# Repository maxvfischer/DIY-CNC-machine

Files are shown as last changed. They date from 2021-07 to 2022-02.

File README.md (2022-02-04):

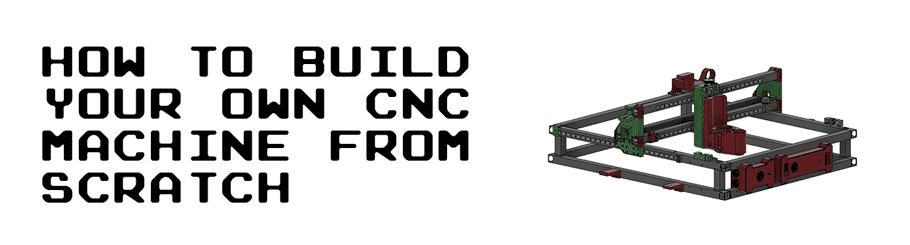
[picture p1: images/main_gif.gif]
main_gif


This guide goes through all the steps to build your own CNC machine from scratch. It includes a complete bill of materials (BOM), STL/OBJ-files for all the 3d-printed parts and detailed instructions of how everything is assembled. It also includes instructions of how all the necessary open-source softwares are installed.

The guide is based on Ivan Miranada's design and is a complement to Ivan's Youtube-videos:

1. Original video: [https://www.youtube.com/watch?v=_atw3e0nIrg](https://www.youtube.com/watch?v=_atw3e0nIrg)
2. Updates with geared stepper motors etc: [https://www.youtube.com/watch?v=qpjf5D3WngY](https://www.youtube.com/watch?v=qpjf5D3WngY)
3. Updating to metal parts: [https://www.youtube.com/watch?v=RDnGvhdGFEY](https://www.youtube.com/watch?v=RDnGvhdGFEY)

If you have any questions, feel free to contact me on LinkedIn: [https://www.linkedin.com/in/max-fischer-92997281/](https://www.linkedin.com/in/max-fischer-92997281/) 

or

contact

cnc_top_gif

---

**Featured on**

* Hackernews (#2): [https://news.ycombinator.com/item?id=29096954](https://news.ycombinator.com/item?id=29096954)
* Console open-source newsletter: [https://console.substack.com/p/console-83](https://console.substack.com/p/console-83)
* Hackaday's blog: [https://hackaday.com/2021/11/05/diy-cnc-uses-lots-of-3d-printed-parts/](https://hackaday.com/2021/11/05/diy-cnc-uses-lots-of-3d-printed-parts/)
* Hackaday's podcast (~25:30): [https://open.spotify.com/episode/2YuxrVAgbQvVTjcUljJ3rj?si=lkp1L061R7ix6WkA7s1ieA](https://open.spotify.com/episode/2YuxrVAgbQvVTjcUljJ3rj?si=lkp1L061R7ix6WkA7s1ieA)
* Arduino's official blog: [https://blog.arduino.cc/2021/11/03/learn-how-to-build-your-own-massive-3d-printed-cnc-router/](https://blog.arduino.cc/2021/11/03/learn-how-to-build-your-own-massive-3d-printed-cnc-router/)
* Weekly robotics newsletter: [https://weeklyrobotics.com/weekly-robotics-168](https://weeklyrobotics.com/weekly-robotics-168)

---

# Table of content
1. [License](#license)
2. [Parts (bill of materials)](#parts-bill-of-materials)
3. [Build the CNC machine](#build-the-CNC-machine)
	1. [Main frame](#main-frame)
		1. [Drill holes in 900 mm profiles](#drill-holes-in-900-mm-profiles)
		2. [Rails to 900 mm profiles](#rails-to-900-mm-profiles)
		3. [Assemble upper and lower frames](#assemble-upper-and-lower-frames)
		4. [Interlock upper and lower frames](#interlock-upper-and-lower-frames)
	2. [Y-axis](#y-axis)
		1. [Side plates to upper frame](#side-plates-to-upper-frame)
		2. [Y-axis motors, idlers and pulleys to side plates](#y-axis-motors-idlers-and-pulleys-to-side-plates)
		3. [Y-axis belt tensioners and end-stop mounts](#y-axis-belt-tensioners-and-end-stop-mounts)
		4. [Y-axis HTD5M belts](#y-axis-htd5m-belts)
	3. [X-axis and Z-axis](#x-axis-and-z-axis)
		1. [Rails to bridge beams](#rails-to-bridge-beams)
		2. [X-axis tensioner and end-stop mount to lower bridge beam](#x-axis-tensioner-and-end-stop-mount-to-lower-bridge-beam)
		3. [Bridge beams to side plates](#bridge-beams-to-side-plates)
		4. [Rod bearings to carriage](#rod-bearings-to-carriage)
		5. [Carriage to bridge beams](#carriage-to-bridge-beams)
		6. [X-axis motor, idlers and pulley to carriage](#x-axis-motor-idlers-and-pulley-to-carriage)
		7. [X-axis HTD5M belt](#x-axis-htd5m-belt)
		8. [Acme nut and rails to carriage slider](#acme-nut-and-rails-to-carriage-slider)
		9. [Acme rod and vertical slider to carriage](#acme-rod-and-vertical-slider-to-carriage)
		10. [Z motor mount and X-axis cable chain](#z-motor-mount-and-X-axis-cable-chain)
		11. [Y-axis cable chain](#y-axis-cable-chain)
		12. [Z stepper motor, pulleys and belt](#z-stepper-motor-pulleys-and-belt)
	4. [Stepper motors and end-stops](#stepper-motors-and-end-stops)
		1. [Extend stepper motor wires](#extend-stepper-motor-wires)
			1. [Y-axis 1](#y-axis-1)
			2. [Y-axis 2](#y-axis-2)
			3. [X-axis](#x-axis)
			4. [Z-axis](#z-axis)
		2. [End-stops and end-stop wires](#end-stops-and-end-stop-wires)
			1. [X-axis (max)](#x-axis-max)
			2. [X-axis (min)](#x-axis-min)
			3. [Y-axis (max)](#y-axis-max)
			4. [Y-axis (min)](#y-axis-min)
			5. [Z-axis (max)](#z-axis-max)
		3. [Stepper motor and end-stop cable management](#stepper-motor-and-end-stop-cable-management)
			1. [Y-axis steppers and X-axis end-stops](#y-axis-steppers-and-x-axis-end-stops)
			2. [X-axis stepper, Z-axis stepper and Z-axis end-stop](#x-axis-stepper-Z-axis-stepper-and-z-axis-end-stop)
	5. [Router](#router)
		1. [Attach router to carriage](#attach-router-to-carriage)
		2. [Router cable management](#router-cable-management)
	6. [Electronic boxes](#electronic-boxes)
		1. [Small electronic box](#small-electronic-box)
		2. [Large electronic box](#large-electronic-box)
	7. [Electrical wiring and connect components](#electrical-wiring-and-connect-components)
		1. [Main power supply](#main-power-supply)
		2. [Prepare power to steppers and connect fans and LED](#prepare-power-to-steppers-and-connect-fans-and-LED)
		3. [Assemble stepper motor drivers and tune VRef](#assemble-stepper-motor-drivers-and-tune-vref)
		4. [Attach Arduino and solder USB cable](#attach-arduino-and-solder-usb-cable)
		5. [Stepper and end-stop cable management to small electronic box](#stepper-and-end-stop-cable-management-to-small-electronic-box)
		6. [Connect steppers to CNC shield](#connect-steppers-to-cnc-shield)
		7. [Connect end-stops to CNC shield](#connect-end-stops-to-cnc-shield)
		8. [Set microstepping](#set-microstepping)
		9. [Router cable management and connect to main power supply](#router-cable-management-and-connect-to-main-power-supply)
		10. [Final test of electrical wiring](#final-test-of-electrical-wiring)
	8. [Wasteboard](#wasteboard)
		1. [Cut out wasteboard](#cut-out-wasteboard)
		2. [Attach wasteboard to CNC](#attach-wasteboard-to-cnc)
	9. [Dust shoe (updated Feb 4, 2022)](#dust-shoe-updated-feb-4-2022)
4. [Software](#software)
	1. [Install CNC software (grbl) on Arduino Uno](#install-cnc-software-grbl-on-arduino-uno)
		1. [Install Arduino Software (IDE)](#install-arduino-software-ide)
		2. [Install GRBL](#install-grbl)
	2. [G-Code sender](#g-code-sender)
		1. [Install G-Code sender](#install-g-code-sender)
		2. [Connect G-Code sender to GRBL](#connect-g-code-sender-to-grbl)
		3. [Adjust GRBL configuration](#adjust-grbl-configuration)
			1. [Enable end-stops/hard limits](#enable-end-stopshard-limits)
			2. [Calculate and set travel resolutions](#calculate-and-set-travel-resolutions)
			3. [Other configurations](#other-configurations)
5. [Final notes](#final-notes)

# License
The following license is included when buying Ivan Miranda's blueprints of the CNC machine:

```
Everything that is in these files that I produced myself, apart from reselling the files, is allowed.
You can print and sell parts, sell machines, sell courses to build the machine. Modify the parts and post 
them for free, as long as you don’t sell the files and keep this license on everything you make with the 
files and credit me, we’re good. No DRM or anything, you are even allowed to repost the files as long as 
they’re kept free. Why buy this then? To support me and keep me encouraged to do more projects like this. 
```

Ivan does an amazing job putting these DIY builds together. I've posted his STL-files in this repository to simplify the build, but PLEASE buy his blueprints here: [https://ivanmiranda.com/products/3d-printed-cnc](https://ivanmiranda.com/products/3d-printed-cnc). It's only \$25 and helps him to continue build and share his awesome projects. Also, you will get access to a Discord channel that is really useful, where you can ask questions to a lot of people who have already built the machine.

Also, the Z-axis end-stop trigger, the ordinary end-stops and the rail supports all come from cello4's GitHub: [https://github.com/4cello/mirandacnc-community](https://github.com/4cello/mirandacnc-community).

# Parts (bill of materials)

**CLICK HERE TO OPEN THE BILL OF MATERIALS (BOM) MARKDOWN: [Bill of materials](./BILLOFMATERIAL.md)**

To simplify the build, I've created a separate markdown page with tables covering all parts needed to build the CNC-machine. The tables include a unique `Item No.` to easier refer to the parts in the guide. The tables also include images of all parts and .STL/.OBJ files of the parts that needs to be 3d-printed.

To get an even better understanding of how all the parts are used, I've created a detailed spreadsheet with comments:

* [On Google drive](https://docs.google.com/spreadsheets/d/1VdnPilA22OfAh9a1y4Ft6c2xkio206Dzv85h7AX7CmQ/edit?usp=sharing)
* [Bill\_of\_material.xlsx](./Bill_of_material.xlsx)

**To be able to continue with the build, you need to buy and 3d-print all needed parts found in the [bill of materials](./BILLOFMATERIAL.md).**

# Build the CNC machine
This section covers how all the parts is put together to build the CNC machine. 

All the measurements, distances and a complete overview of how everything comes together can be found in the main Fusion 360 CAD design. It can be downloaded here:

* [fusion\_360\_cad\_files.f3z](./fusion_360_cad_files.f3z)

Please note that the main Fusion 360 design is quite messy, which is one of the reasons why I've extracted the needed parts in a separate bill of materials.

Fusion 360 is a CAD program developed by Autodesk. It's free for personal use and can be downloaded here: [https://www.autodesk.com/products/fusion-360/personal](https://www.autodesk.com/products/fusion-360/personal). After you've downloaded Fusion 360, import `fusion_360_cad_files.f3z` to load the main CAD design. This can also come in handy if you need to adjust some of the 3d-printed parts.

## Main frame

### Drill holes in 900 mm profiles
The main frame consists of two separate frames, the lower and the upper frame. The two frames are kept together using threaded rods, washers and nuts. To enable the threaded rods to slide through the aluminium profiles, holes needed to be drilled.

First, a sharpie was used to indicate where all the holes were going in the 900mm profiles (**O07**). This was done by using a set square and a penn. A bradawl and a hammer were then used to make indentations at the center of the holes.

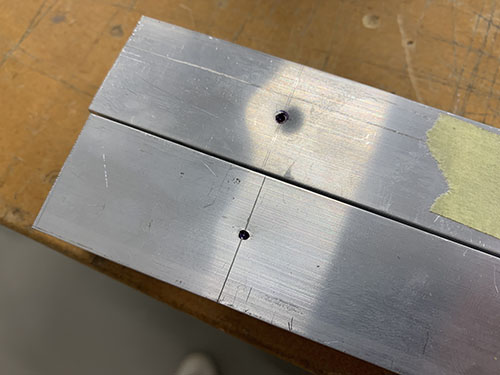
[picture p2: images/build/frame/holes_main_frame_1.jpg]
holes_main_frame_1


A 9 mm drill-bit and a bench drill was used to drill the holes straight through the profiles.

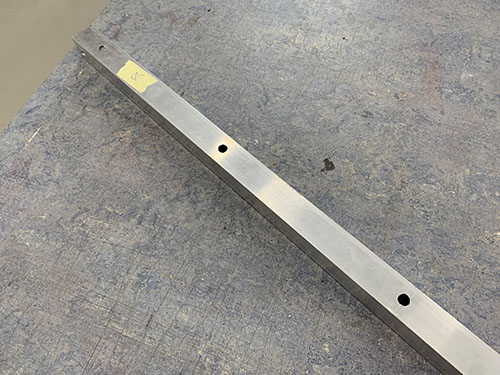
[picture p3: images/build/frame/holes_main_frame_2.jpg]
holes_main_frame_1


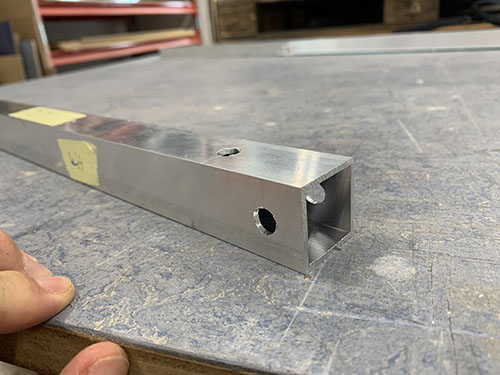
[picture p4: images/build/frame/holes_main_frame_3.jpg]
holes_main_frame_1


To be able to access the nuts and tight them with a socket wrench, some holes (facing outwards, see Fusion360 CAD file) needed to be enlarged. A sharpie was used to mark all the holes that needed to be enlarged.

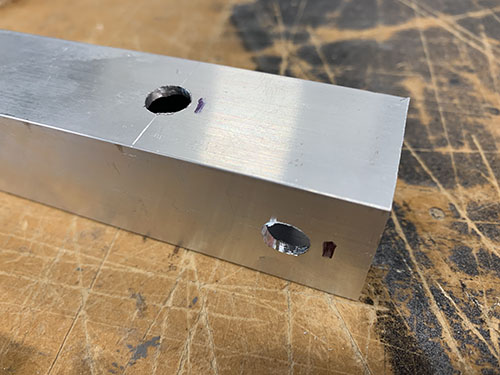
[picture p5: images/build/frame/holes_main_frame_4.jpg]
holes_main_frame_1


A step drill was then used to enlarge the holes holes to 20 mm. A tip is to measure the size of your socket wrench and keep the holes as small as possible, while you're still able to tighten the nuts. To be able to see which step you're aiming for on the step drill, attach a small piece of masking tape on the step above.

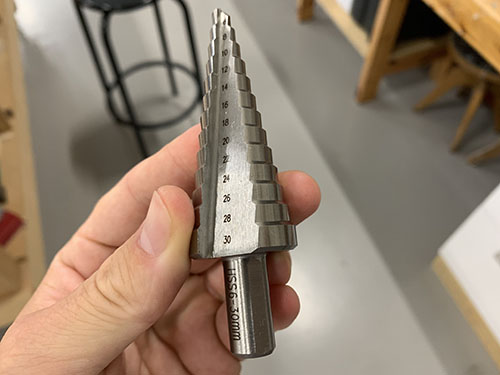
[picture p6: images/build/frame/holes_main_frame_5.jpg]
holes_main_frame_1


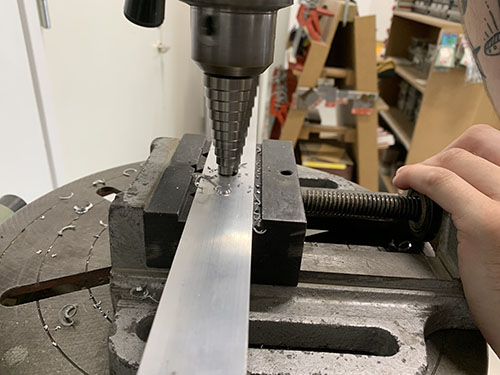
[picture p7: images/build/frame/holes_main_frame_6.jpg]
holes_main_frame_1


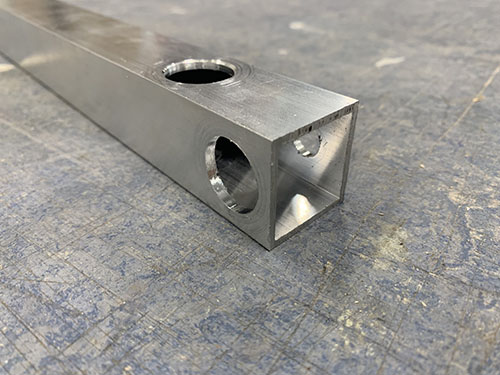
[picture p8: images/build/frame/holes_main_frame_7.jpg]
holes_main_frame_1


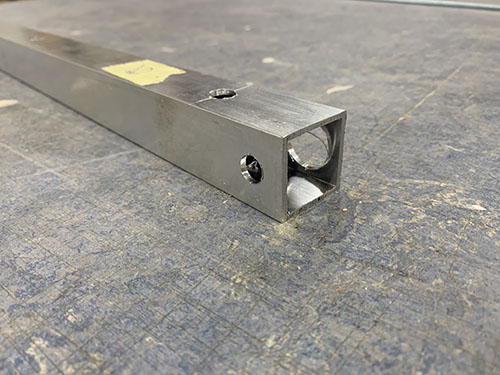
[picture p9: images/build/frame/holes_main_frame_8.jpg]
holes_main_frame_1


The edges were finally smoothed out using a round metal file.

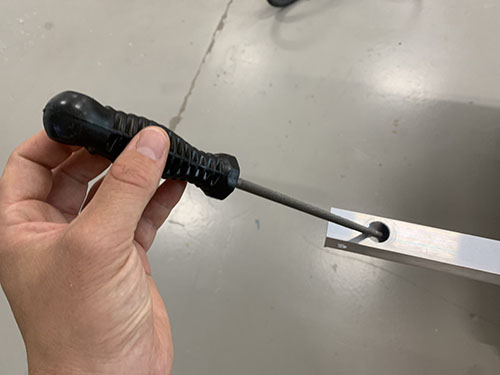
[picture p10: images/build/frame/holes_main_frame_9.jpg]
holes_main_frame_1


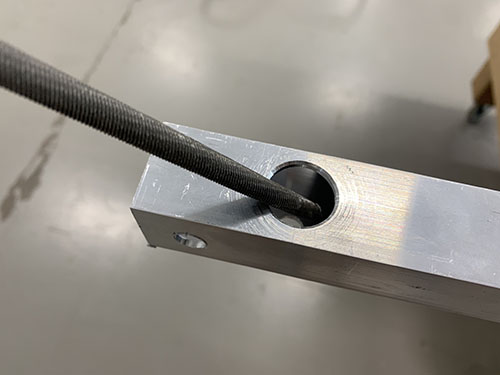
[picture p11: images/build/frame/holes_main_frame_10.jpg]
holes_main_frame_1


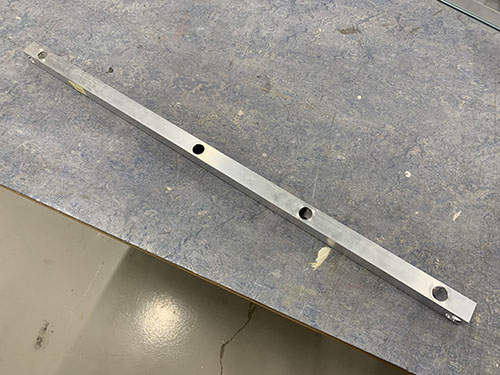
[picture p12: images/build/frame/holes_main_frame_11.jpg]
holes_main_frame_1


### Rails to 900 mm profiles

Before the upper and lower frames were assembled, two 600 mm MGN12H rails (**O21**) were attached to the 900 mm aluminium profiles (**O07**) of the **upper** frame. They were attached to the sides facing outwards and above the three 80 mm vertical beams (connecting the lower and upper frame). A tip is to place all the profiles as they should go to make sure that you're attaching the rails to the correct faces (see the red boxes on the image below). Also, be very careful when removing the MGN12H blocks (**O22**) from the rails.

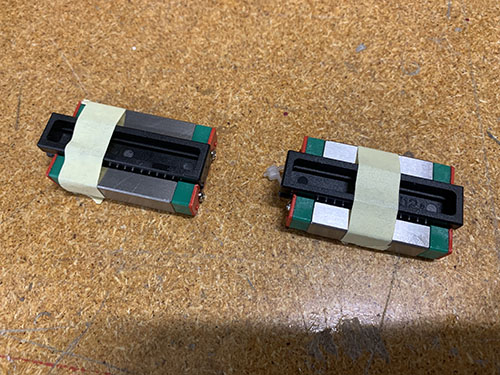
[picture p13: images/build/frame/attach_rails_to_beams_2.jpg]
attach_rails_to_beams_2


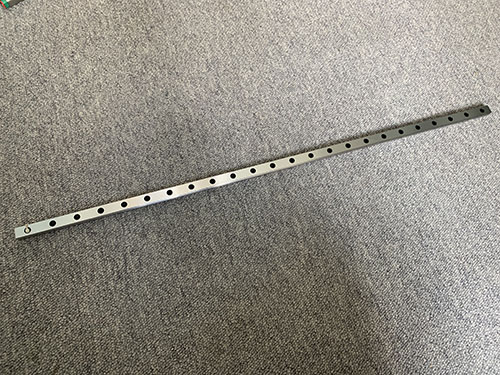
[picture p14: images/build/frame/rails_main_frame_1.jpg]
rails_main_frame_1


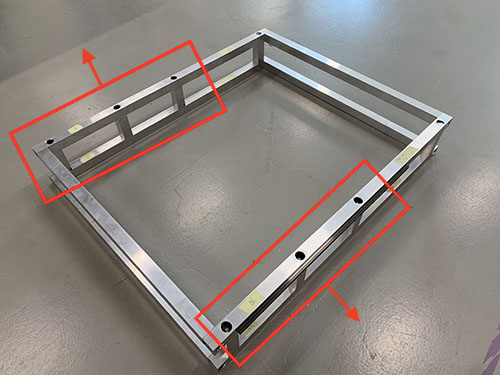
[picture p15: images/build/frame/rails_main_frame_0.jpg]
rails_main_frame_0


3x 3d-printed support tools (**P25**) were used to center the rails on the profiles. A 57 mm wood block were cut out and used to attach the rails at the same distance from the end of the profiles on both sides. The rails were then clamped to the profiles.

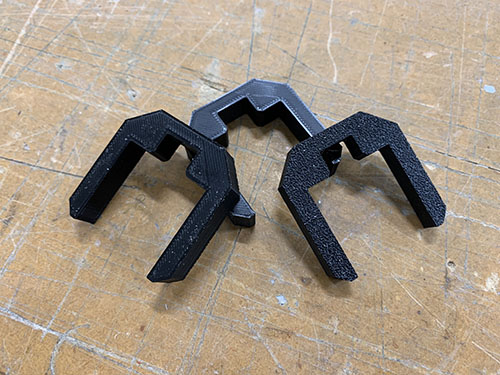
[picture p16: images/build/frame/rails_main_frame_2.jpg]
rails_main_frame_2


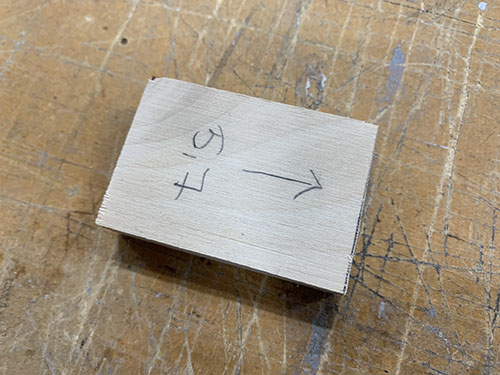
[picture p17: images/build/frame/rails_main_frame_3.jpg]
rails_main_frame_3


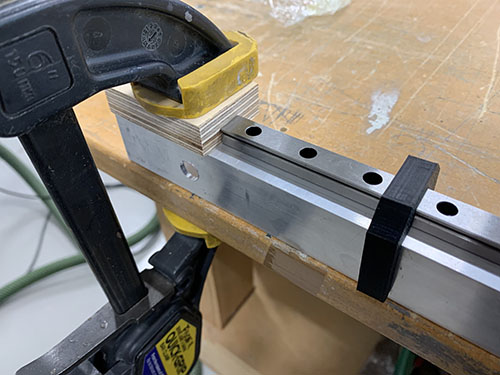
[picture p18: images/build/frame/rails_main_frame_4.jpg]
rails_main_frame_4


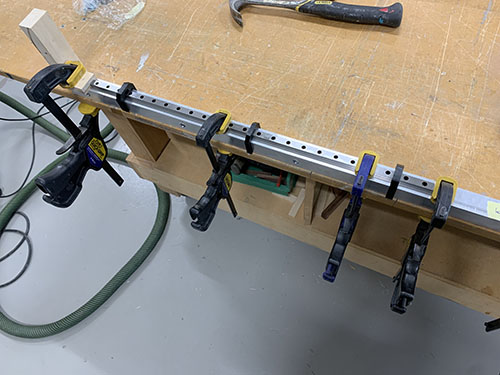
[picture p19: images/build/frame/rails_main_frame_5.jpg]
rails_main_frame_5


A bradawl and a hammer were then used to make indentations at the center of the holes. Cutting fluid was applied and a 2 mm drill was used to drill all the holes.

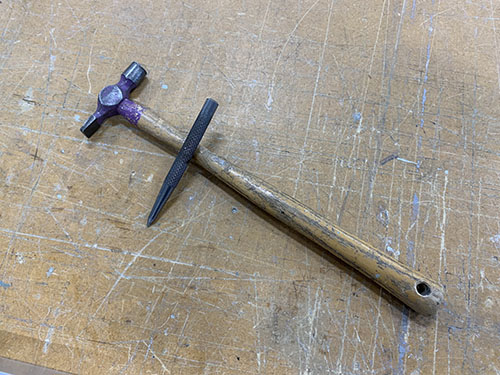
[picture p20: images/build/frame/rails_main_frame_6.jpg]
rails_main_frame_6


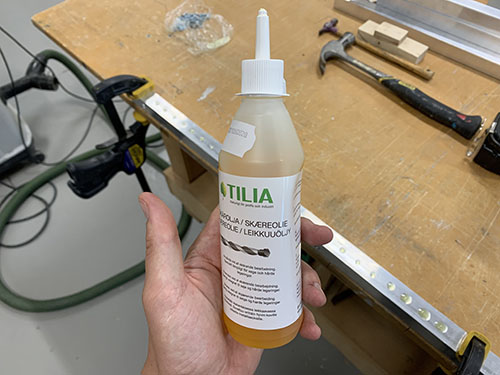
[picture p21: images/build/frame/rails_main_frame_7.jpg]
rails_main_frame_7


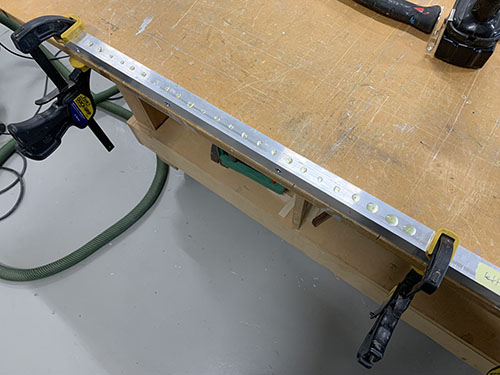
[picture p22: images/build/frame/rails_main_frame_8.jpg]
rails_main_frame_8


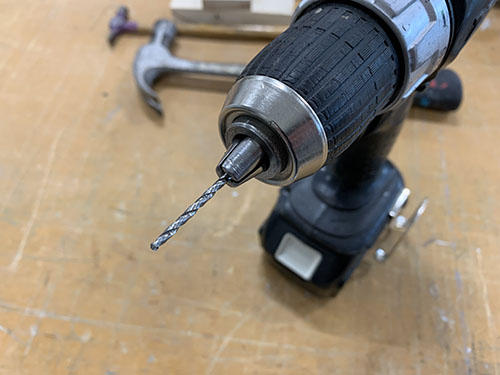
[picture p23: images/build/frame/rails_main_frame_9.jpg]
rails_main_frame_9


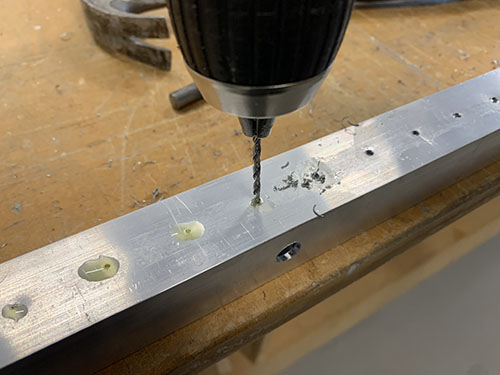
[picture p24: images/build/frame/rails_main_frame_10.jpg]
rails_main_frame_10


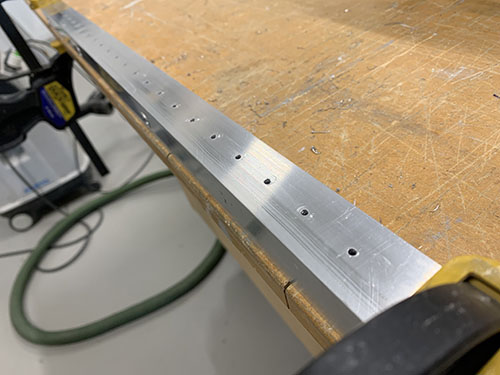
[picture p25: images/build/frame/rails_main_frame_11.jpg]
rails_main_frame_11


Cutting fluid was then applied once more on the drilled holes and a M3 drill tap was used to create threads in the holes.

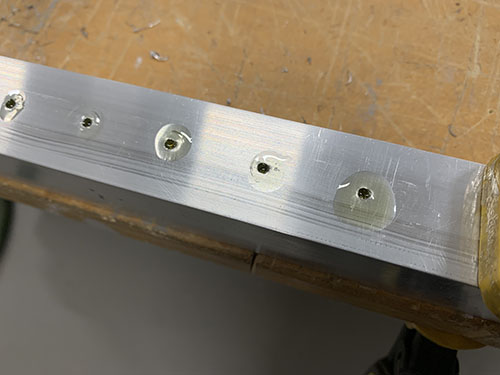
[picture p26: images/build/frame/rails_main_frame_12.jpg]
rails_main_frame_12


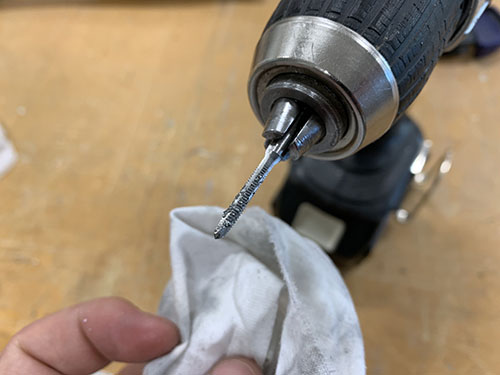
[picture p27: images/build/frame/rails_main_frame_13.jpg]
rails_main_frame_13


Finally, the rails were attached using 48x 16 mm M3 screws (**S03**).

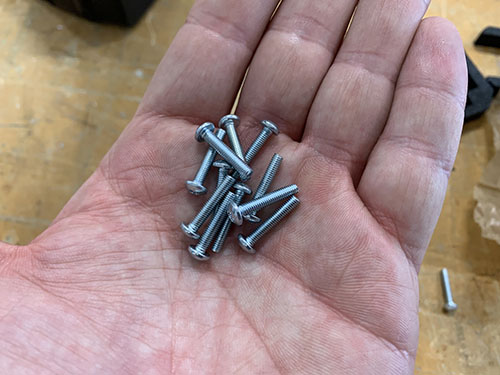
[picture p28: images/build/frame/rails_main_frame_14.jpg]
rails_main_frame_14


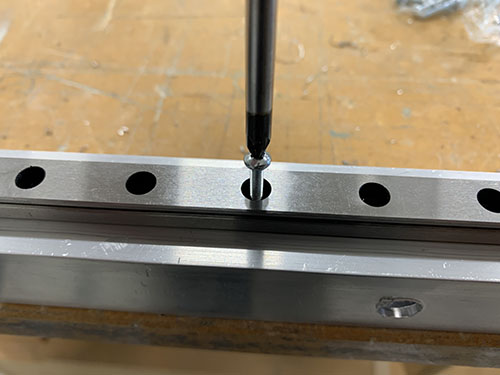
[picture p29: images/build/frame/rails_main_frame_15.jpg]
rails_main_frame_15


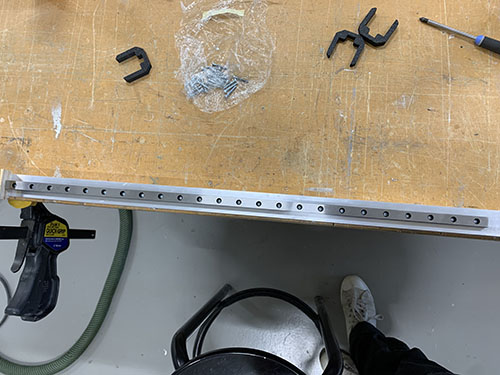
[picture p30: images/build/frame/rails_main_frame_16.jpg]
rails_main_frame_16


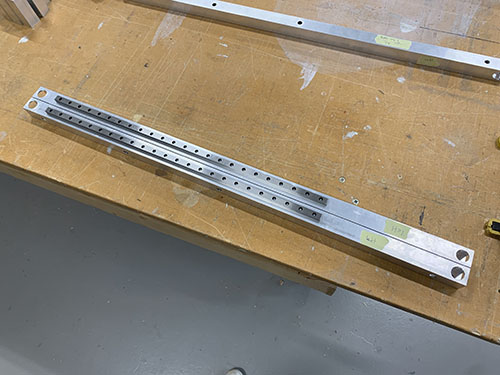
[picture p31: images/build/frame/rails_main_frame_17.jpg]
rails_main_frame_17


### Assemble upper and lower frames

The two frames were assembled using the 4x 717 mm M8 threaded rods (**T03**), 8x (20mm, 10mm, 2mm) washers (**W04**) and 8x M8 lock nuts (**N03**).

The profiles were first placed in their correct place and clamps were used to keep the profiles aligned. I used two jointed spanners (one one each side) to lock everything in place, but you can also use two socket wrenches. Just make sure that the bits fit into the drilled holes.

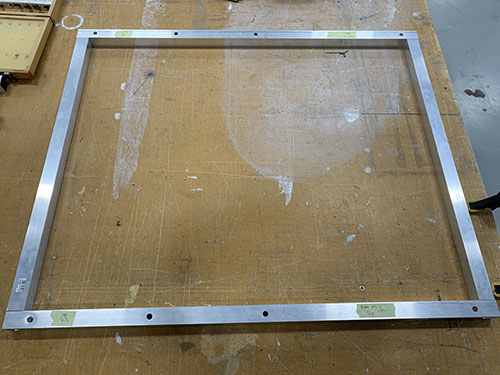
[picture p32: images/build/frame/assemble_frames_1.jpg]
assemble_frames_1


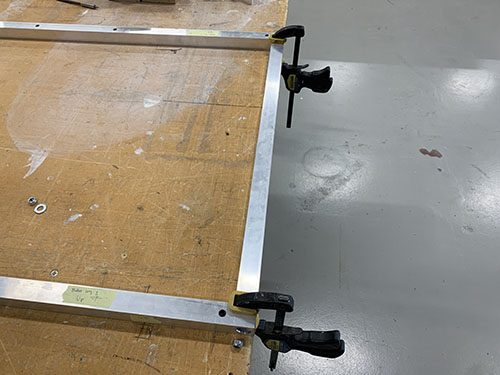
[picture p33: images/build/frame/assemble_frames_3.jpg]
assemble_frames_3


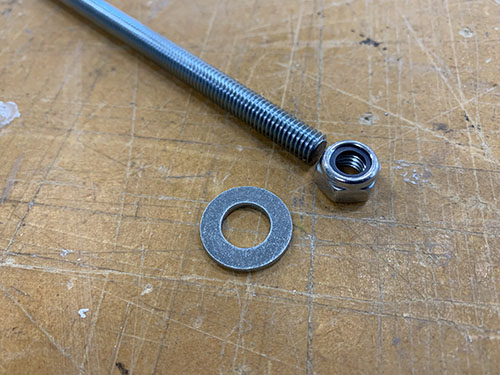
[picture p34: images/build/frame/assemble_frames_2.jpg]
assemble_frames_2


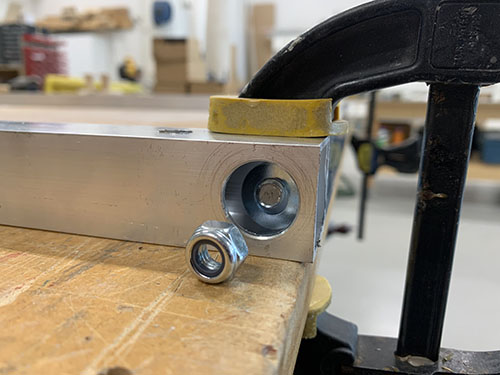
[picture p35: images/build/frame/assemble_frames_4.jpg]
assemble_frames_4


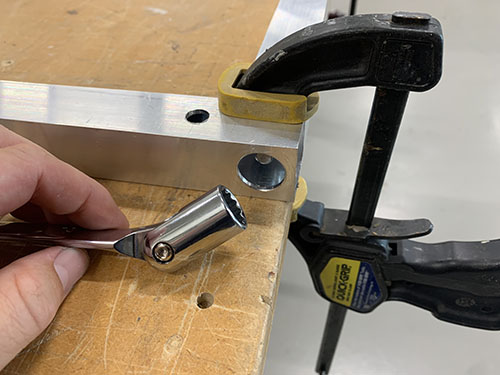
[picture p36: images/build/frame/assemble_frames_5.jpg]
assemble_frames_5


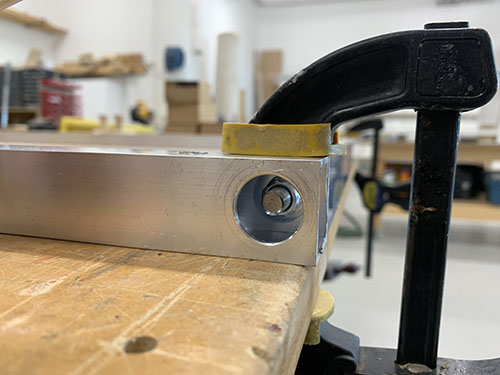
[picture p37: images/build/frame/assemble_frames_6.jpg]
assemble_frames_6


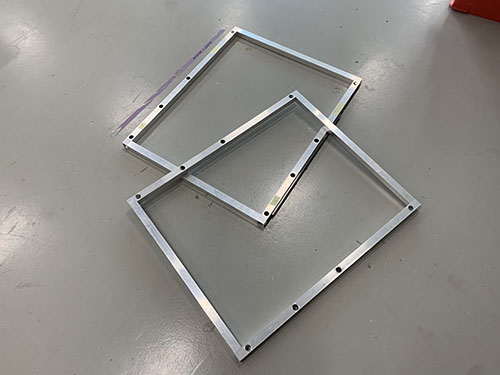
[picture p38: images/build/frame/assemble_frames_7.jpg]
assemble_frames_7


### Interlock upper and lower frames

The upper and lower frames and the 8x 80 mm vertical aluminium beams (**O06**) were first layed out in their correct place. The 803 mm horizontal bridge beams (used later in the tutorial) (**O05**) and clamps were then used to align the frames on top of each other.

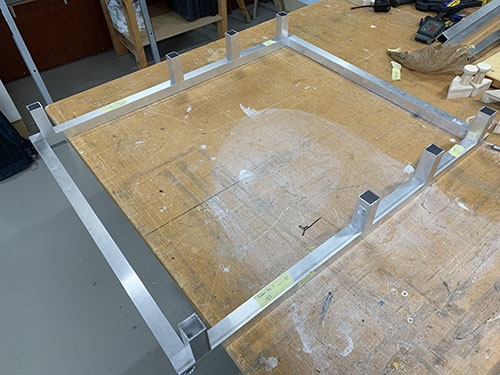
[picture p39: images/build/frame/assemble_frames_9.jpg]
assemble_frames_9


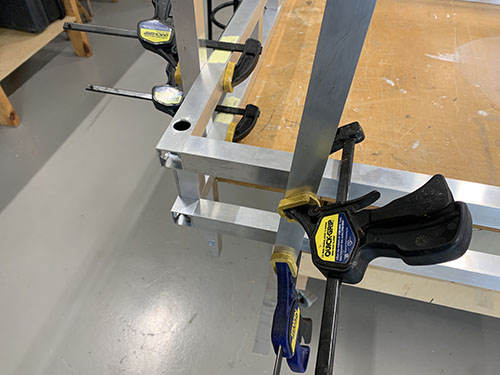
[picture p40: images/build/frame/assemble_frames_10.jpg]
assemble_frames_10


8x 120 mm M8 threaded rods (**T02**), 16x (20mm, 10mm, 2mm) washers (**W04**) and 16x M8 lock nuts (**N03**) were then used to interlock the upper and lower frames, with the 80 mm vertical aluminium profiles in between.

assemble_frames_8

assemble_frames_12

assemble_frames_11

assemble_frames_13

## Y-axis

### Side plates to upper frame

Before attaching the side plates, the MGN12H blocks (**O22**) were added back onto the rails, 2x on each side. Be careful when sliding them onto the rails, there are multiple small bearing balls that easily fall out of the blocks.

assemble_side_plates_1

assemble_side_plates_2

The left (**P20**) and right (**P29**) side plates where then attached to the blocks using 16x 20 mm M3 screws (**S04**) (8x on each side plate). Make sure to attach the plates on the correct side (see images below).

I had to redesign the left side plate and reprint it later in the build (after the images were taken). Therefore, the left side plate seen in the upcoming images look a bit different than the one used (see next image for the left side plate used).

assemble_side_plates_3

assemble_side_plates_4

assemble_side_plates_5

assemble_side_plates_6

assemble_side_plates_7

assemble_side_plates_8

### Y-axis motors, idlers and pulleys to side plates

Each idler were made up out of 1x idler blocker (**P16**), 2x 60 mm fully threaded M8 screws (**S15**), 6x 698zz bearings (**O01**) and 8x (15 mm x 8.5 mm x 1.5mm) washers (**W03**) (2x closest to the idler blocker and 6x closest to the side plate). The idlers were then attached to each side plate using two M8 nuts (**N03**). Make sure that the bearings are spinning freely.

attach_side_plate_motors_1

attach_side_plate_motors_2

As I designed and added the idler blocker later on in the build, some of the images doesn't have it and they also have 3x washers instead of 1x washer closest to the screw head. I left these images anyways in the guide so you can see how it looks when you attach the idlers, but please ignore the wrong number of washers. Also ignore all the other things around the idlers in the upcoming 2 images, they are taken later on in the build.

attach_side_plate_motors_3_0

attach_side_plate_motors_3_1

Should be idler blockers and a different number of washers in the upcoming images.

attach_side_plate_motors_3

attach_side_plate_motors_4

attach_side_plate_motors_5

attach_side_plate_motors_6

attach_side_plate_motors_7

To attach the stepper motors to the side plates, the 4x M3 screws (**S07**) locking the gear box to the motor were removed. Save these as they will be used later on to attach the power supply and Arduino to the electronic boxes.

attach_side_plate_motors_1

attach_side_plate_motors_1

The 2x geared stepper motors (**E18**) were then inserted into the large holes on the side plates, facing inwards. 4x 40 mm M3 screws (**S06**) and 4x M3 washers (**W05**) were used to lock each stepper motor to the side plates (I forgot to add the washers in the images below, therefore they're not visible). The motors should be attached so that the cables are facing in the direction of the two bridge beams (i.e. the longer vertical surface on the side plates).

attach_side_plate_motors_1

attach_side_plate_motors_1

attach_side_plate_motors_1

attach_side_plate_motors_1

attach_side_plate_motors_1

1x HTD5M timing pulley (**O18**) was attached to each motor shaft using set screws.

attach_side_plate_motors_1

attach_side_plate_motors_1

attach_side_plate_motors_1

attach_side_plate_motors_1

### Y-axis belt tensioners and end-stop mounts

2x fixed belt tensioners (**P19**, **P28**) were attached to the longer aluminium profiles of the upper frame using 4x 20mm M5 screws (**S12**) (2x for each fixed belt tensioner). When aligning the fixed belt tensioners, make sure that the "belt opening" is pointing in the direction of the rails (1x fixed belt tensioner for each rail). Also make sure that the fixed belt tensioners are positioned on the correct side of the rail (see images). Similar to before, a bradawl and a hammer were used to make indentations at the center of the holes. Cutting fluid was applied and a 4 mm drill was used to drill the holes, followed by a M5 drill tap.

attach_tensioners_and_belts_12

attach_tensioners_and_belts_13

attach_tensioners_and_belts_14

attach_tensioners_and_belts_15

attach_tensioners_and_belts_16

attach_tensioners_and_belts_17

attach_tensioners_and_belts_18

2x belt tension sliders (**P17**, **P26**) were attached on the opposite side of the fixed belt tensioners, ontop of the aluminium profile, using 4x 20mm M5 screws (**S12**). To get them aligned at the exact same place on both sides, a 100 mm distance was cut out and a flat support was clamped to the inner side of the profile. The same drill and tap size were used as for the fixed belt tensioners (4mm drill, M5 drill tap). Make sure that the belt tension sliders are pointing outwards.

attach_tensioners_and_belts_19

attach_tensioners_and_belts_20

attach_tensioners_and_belts_21

attach_tensioners_and_belts_22

attach_tensioners_and_belts_23

attach_tensioners_and_belts_24

attach_tensioners_and_belts_25

attach_tensioners_and_belts_26

attach_tensioners_and_belts_27

2x end-stop mounts (**P08**) were then attached to the same side as the belt tension sliders using 4x 20mm M5 screws (**S12**), facing outwards and aligned with the rails. The same drill and tap size were used as for the fixed belt tensioners (4mm drill, M5 drill tap).

attach_tensioners_and_belts_1

attach_tensioners_and_belts_2

attach_tensioners_and_belts_3

attach_tensioners_and_belts_4

attach_tensioners_and_belts_5

attach_tensioners_and_belts_6

attach_tensioners_and_belts_7

attach_tensioners_and_belts_8

attach_tensioners_and_belts_9

attach_tensioners_and_belts_10

attach_tensioners_and_belts_11

The belt tensioners (**P18**, **P27**) were loosely attached to the belt tension sliders using 2x 60 mm fully threaded M8 screws (**S15**), 2x M8 nuts(**N03**) and 2x (20mm x 10mm x 2mm) washers (**W04**).

attach_tensioners_and_belts_28

attach_tensioners_and_belts_29

### Y-axis HTD5M belts

The HTD5M belt (**O17**) was first inserted into one of the fixed belt tensioners using a flat screw driver. It was then stretched along the aluminium profile, below the first idler, around the timing pulley, below the second idler and all the way to the belt tensioner.

attach_tensioners_and_belts_30

attach_tensioners_and_belts_31

attach_tensioners_and_belts_32

attach_tensioners_and_belts_33

attach_tensioners_and_belts_34

A scissor was used to cut the belt at an appropriate length. The loose end was then inserted into the belt tensioner using a flat screw driver and the belt was stretched by tightning the M8 nut.

attach_tensioners_and_belts_35

attach_tensioners_and_belts_36

attach_tensioners_and_belts_37

attach_tensioners_and_belts_38

attach_tensioners_and_belts_39

Make sure that the belt is not too loose and not too tight.

attach_tensioners_and_belts_40

attach_tensioners_and_belts_41

Repeat on the other side.

## X-axis and Z-axis

### Rails to bridge beams

The last two 600 mm MGN12H rails (**O21**) were attached to two of the 803 mm aluminium bridge beams (**O05**, used for the X-axis). First, the MGN12H blocks (**O22**) were carefully removed from the rails.

attach_rails_to_beams_1

attach_rails_to_beams_2

The same 100 mm distance used to align the belt tension sliders were used to align the rails. Because they will be off center by 3 mm, make sure that you later attach the bridge beams to the side plates in a way so the rails line up. 

The same 3d-printed support tools (**P25**) used to align the rails on the 900 mm aluminium profiles were used here as well. Everything was clamped into position. A bradawl and a hammer were used to make indentations and a 2 mm drill and a M3 drill tap was used to make the screw holes.

attach_rails_to_beams_3

attach_rails_to_beams_4

attach_rails_to_beams_5

attach_rails_to_beams_6

attach_rails_to_beams_7

attach_rails_to_beams_8

attach_rails_to_beams_9

attach_rails_to_beams_10

attach_rails_to_beams_11

The rails were finally attached using 16 mm M3 screws (**S03**) and the MGN12H  rail blocks (**O22**) were gently slided back onto the rails.

attach_rails_to_beams_12

attach_rails_to_beams_13

attach_rails_to_beams_14

attach_rails_to_beams_15

### X-axis tensioner and end-stop mount to lower bridge beam

The fixed tensioner (**P28**) and end-stop mount (**P08**) were attached to the lower bridge beam in the same fashion as on the 900 mm aluminium profiles, using 4x 20mm M5 screws (**S12**). When aligning the fixed tensioner, make sure that the "belt opening" is pointing in the direction of the rail. A bradawl and a hammer were used to make indentations at the center of the holes. Cutting fluid was applied and a 4 mm drill was used to drill the holes, followed by a M5 drill tap.

attach_tensioners_to_beams_1

attach_tensioners_to_beams_2

attach_tensioners_to_beams_3

attach_tensioners_to_beams_4

attach_tensioners_to_beams_5

attach_tensioners_to_beams_6

attach_tensioners_to_beams_7

attach_tensioners_to_beams_8

attach_tensioners_to_beams_9

attach_tensioners_to_beams_10

attach_tensioners_to_beams_11

attach_tensioners_to_beams_12

### Bridge beams to side plates

All three bridge beams (**O05**) were then inserted into the slots on the side plates. Make sure that the two beams with the rails are on top of each other, with the rails pointing outwards. Also, make sure that you insert them in the correct orientation, so that the rails are lined up (due to the rails being 3 mm off center).

attach_beams_to_side_plates_1

attach_beams_to_side_plates_1

attach_beams_to_side_plates_1

attach_beams_to_side_plates_1

When the bridge beams were aligned, the blocker clips (**P21**, **P22**, **P23**, **P30**, **P31**, **P32**) were placed in their correct place and a sharpie was used to mark the center of the holes to be drilled. Similar to before, a bradawl and a hammer were used to make indentations at the center of the holes.

attach_beams_to_side_plates_1

attach_beams_to_side_plates_1

attach_beams_to_side_plates_1

attach_beams_to_side_plates_1

A 7 mm drill bit was used to drill the holes. As these holes were going straight through the profiles, a bench drill was used for precision. A metal file was used to remove all excess metal around the holes.

attach_beams_to_side_plates_1

attach_beams_to_side_plates_1

The bridge beams were then inserted into the slots on the side plates once more, along with all the blocker clips. 2x 140 mm threaded M5 rod (**T01**) was inserted through the bottom two beams and 2x 60 mm M5 (**S14**) screws was inserted through the top bridge beam. It was all tightened using M5 nuts (**N02**).

attach_beams_to_side_plates_1

attach_beams_to_side_plates_1

attach_beams_to_side_plates_1

attach_beams_to_side_plates_1

attach_beams_to_side_plates_1

attach_beams_to_side_plates_1

attach_beams_to_side_plates_1

### Rod bearings to carriage

Before attaching the carriage (**P07**) to the bridge beams, two KFL08 rod bearings (**O19**) were attached on the top and the bottom of the carriage (inside) using 4x 20 mm M5 screws (**S12**) and 4x M5 nuts (**N02**). A tip is to temporarily use the acme rod (used in an upcoming step) to vertically align the two bearings.

assemble_carriage_1

assemble_carriage_2

assemble_carriage_3

assemble_carriage_4

assemble_carriage_5

### Carriage to bridge beams

The carriage was attached to the 4x MGN12H blocks (**O22**) on the bridge beams, using 16x 25 mm M3 screws (**S05**).

attach_carriage_to_beams_1

attach_carriage_to_beams_2

attach_carriage_to_beams_3

attach_carriage_to_beams_4

### X-axis motor, idlers and pulley to carriage

Each idler were made up out of 1x 60 mm fully threaded M8 screw (**S15**), 3x 698zz bearings (**O01**) and 4x (15 mm x 8.5 mm x 1.5mm) washers (**W03**) (1 closest to the idler blocker and 3 closest to the side plate). 2x idlers were then attached to each side plate using 2x M8 nuts (**N03**). Make sure that the bearings are spinning freely.

attach_side_plate_motors_1

attach_side_plate_motors_2

As I designed and added the idler blocker later on in the build, some of the images doesn't have it and they also have 3 washers instead of 1 washer closest to the screw head. I left these images anyways in the guide so you can see how it looks when you attach the idlers, but please ignore the wrong number of washers. Also ignore all the other things around the idlers in the upcoming image, they are taken later on in the build.

attach_idlers_motor_to_carriage_3

Should be idler blockers and a different number of washers in the upcoming images.

attach_idlers_motor_to_carriage_3

attach_idlers_motor_to_carriage_4

attach_idlers_motor_to_carriage_5

To attach the stepper motor to the carriage, the 4x M3 screws locking the gear box to the motor were removed.

attach_idlers_motor_to_carriage_6

attach_idlers_motor_to_carriage_7

attach_idlers_motor_to_carriage_8

The stepper motor was then inserted into the large hole on the carriage, facing towards the bridge beams/idlers. 4x 40 mm M3 screws (**S06**) and 4x M3 washers (**W05**) were used to lock the stepper motor onto the carriage. The motor should be attached so that the cables are facing upwards.

attach_idlers_motor_to_carriage_9

attach_idlers_motor_to_carriage_10

attach_idlers_motor_to_carriage_11

1x HTD5M timing pulley (**O18**) was attached to the motor shaft using set screws.

attach_idlers_motor_to_carriage_12

attach_idlers_motor_to_carriage_13

### X-axis HTD5M belt

The HTD5M belt (**O17**) was first inserted into the fixed belt tensioner using a flat screw driver. It was then stretched along the aluminium profile, below the first idler, around the timing pulley, below the second idler and all the way to the other side.

The belt was cut at an appropriate length and inserted into the belt tensioner (**P27**) using a flat screw driver.

attach_x_axis_belt_1

attach_x_axis_belt_2

attach_x_axis_belt_3

attach_x_axis_belt_4

attach_x_axis_belt_5

The belt tensioner was then attached to the side plate using 1x 60mm fully threaded M8 screw (**S15**), 1x M8 nut (**N03**) and 1x (20mm x 10mm x 2mm) washer (**W04**). The M8 screw in the image is not fully threaded as I lost the one I was suppose to use and had to use another one, so please ignore :)

attach_x_axis_belt_6

attach_x_axis_belt_7

Make sure that the belt is not too loose and not too tight.

attach_x_axis_belt_8

### Acme nut and rails to carriage slider

1x acme nut (**O03**) was inserted from the outside, into the the center hole at the top of the vertical carriage slider (**P36**). It was locked in place using 4x 25mm M3 screws (**S05**).

assemble_carriage_6

assemble_carriage_6

assemble_carriage_7

assemble_carriage_8

2x smaller 200 mm MGN12H rails (**O20**) were then attached to the back of the vertical carriage slider. First, the MGN12H blocks (**O22**) were carefully removed from each rail. After that, the rails were screwed in place on the back of the vertical carriage slider using 16x 20 mm M3 screws (**S04**). The MGN12H blocks were then slided back on and each end were blocked using tape. 

assemble_carriage_9

assemble_carriage_10

assemble_carriage_11

assemble_carriage_12

assemble_carriage_13

### Acme rod and vertical slider to carriage

To attach the vertical slider to the carriage, 16x 25 mm M3 screws (**S05**) were first inserted into the holes on the carriage. You might need to "open up" the holes using a narrow tool (depending on the direction you 3d-printed the carriage).

assemble_carriage_17

assemble_carriage_18

assemble_carriage_19

1x acme rod (**O02**) was then inserted through the two KFL08 rod bearings and the acme nut, and the set screws on the bearings were tightened.

assemble_carriage_14

assemble_carriage_15

assemble_carriage_16

The vertical slider was finally attached to the carriage by attaching the previously mentioned 16x 25 mm M3 screws (**S05**) to the MGN12H blocks on the vertical slider.

assemble_carriage_20

assemble_carriage_21

### Z motor mount and X-axis cable chain

The first step was to find a good length of the X-axis cable chain (**O09**). To simplify this process, the X-axis belt was removed to easier move the carriage along the X-axis.

assemble_carriage_22

The Z motor mount (**P40**) and the X-axis cable chain mount (**P38**) were then attached using 3x 25 mm M4 screws (**S10**), 3x M4 nuts (**N01**) and 3x (10mm x 5mm x 1mm) washers (**W01**).

assemble_carriage_23

assemble_carriage_24

assemble_carriage_25

assemble_carriage_26

assemble_carriage_27

assemble_carriage_28

assemble_carriage_29

assemble_carriage_30

They Z motor mount was then attached to the carriage using 2x 80mm M8 screws (**S16**), 2x M8 nuts (**N03**) and 1x (20mm x 10mm x 2mm) washers (**W04**). The vaccum mount was also inserted and attached to the right-side M8 screw. Please ignore the timing pulley attached to the acme rod in some of the images, it will be attached in a later step.

assemble_carriage_30

assemble_carriage_31

assemble_carriage_32

assemble_carriage_33

assemble_carriage_34

assemble_carriage_35

1x 1 meter cable chain (**O09**) were then clamped to the cable chain mount and to the back-side bridge beam. The carriage was then moved as far to the sides as possible. It's important that the chain doesn't touch any of the side plates when moved. In my case, I had to remove 3 links from the cable chain to get a good length of the chain.

assemble_carriage_36

assemble_carriage_37

assemble_carriage_38

assemble_carriage_39

assemble_carriage_39

The Z motor mount and cable chain mount were then disassembled and the cable chain was properly attached to the cable chain mount using 2x 25mm M4 screws (**S10**), 2x M4 nuts (**N01**) and 2x (10mm x 5mm x 1mm) washers (**W01**).

assemble_carriage_40

assemble_carriage_41

assemble_carriage_42

assemble_carriage_43

The Z motor mount and cable chain mount were then assembled again and attached to the carriage in the same fashion as before.

assemble_carriage_44

assemble_carriage_45

assemble_carriage_46

assemble_carriage_47

The carriage was move all the way to the right side plate and the cable chain was clamped to the lower back bridge beam.

assemble_carriage_48

assemble_carriage_49

A bradawl and a hammer were used to make indentations at the center of the two holes. Cutting fluid was applied and a 3 mm drill was used to drill the holes, followed by a M4 drill tap. The cable chain was then attached to the bridge beam using 2x 25 mm M4 screws (**S10**).

assemble_carriage_50

assemble_carriage_51

assemble_carriage_52

assemble_carriage_53

assemble_carriage_54

assemble_carriage_55

assemble_carriage_56

assemble_carriage_57

assemble_carriage_58

assemble_carriage_59

assemble_carriage_60

Finally, the X-axis belt was reattached and tightened.

assemble_carriage_61

### Y-axis cable chain

The Y-axis cable chain (**O09**) was attached to the frame using 1x cable chain mount (**P05**) and 1x cable chain support (**P06**). The cable chain mount was clamped to the left side of the lower frame and aligned with the last vertial beam. A bradawl and a hammer were used to make indentations at the center of the two holes. Cutting fluid was applied and a 4 mm drill was used to drill the holes, followed by a M5 drill tap. The cable chain mount was then attached to the lower frame using 2x 20 mm M5 screws (**S12**).

assemble_cable_support_y_axis_1

assemble_cable_support_y_axis_2

assemble_cable_support_y_axis_3

assemble_cable_support_y_axis_4

assemble_cable_support_y_axis_5

The cable chain support was only attached to the lower frame for the cable chain to rest on. It was aligned and attached it at the center between the second and third vertical beam. Make sure that it does not go below the bottom frame!

In the same way as the cable chain mount, a bradawl and a hammer were used to make indentations at the center of the two holes. Cutting fluid was applied and a 4 mm drill was used to drill the holes, followed by a M5 drill tap. The support was then attached to the lower frame using 2x 20 mm M5 screws (**S12**).

assemble_cable_support_y_axis_6

assemble_cable_support_y_axis_6

assemble_cable_support_y_axis_7

assemble_cable_support_y_axis_8

assemble_cable_support_y_axis_9

assemble_cable_support_y_axis_10

assemble_cable_support_y_axis_11

The Y-axis cable chain (**O09**) was then attached to the left side plate (**P20**) and lower frame support using 4x 25 mm M4 screws (**S10**), 4x M4 nuts (**N01**) and 4x (10mm x 5mm x 1mm) washers (**W01**).

assemble_cable_support_y_axis_12

assemble_cable_support_y_axis_13

assemble_cable_support_y_axis_14

assemble_cable_support_y_axis_15

assemble_cable_support_y_axis_16

assemble_cable_support_y_axis_17

### Z stepper motor, pulleys and belt

The non-geared NEMA17 stepper motor (**E11**) was attached to the Z-axis motor mount using 4x 8mm M3 screws (**S08**) and 4x M3 washers (**W06**). Make sure that the motor cable connector is pointing in the same direction as the opening of the X-axis cable chain.

1x 16 teeth GT2 timing pulley (**O15**) was then attached to the motor shaft and 1x 60 teeth GT2 timing pulley (**O16**) was attached to the acme rod. Both were locked in place using set screws. Make sure that they line up. 

attach_z_stepper_pulleys_belt_1

attach_z_stepper_pulleys_belt_2

attach_z_stepper_pulleys_belt_3

attach_z_stepper_pulleys_belt_4

attach_z_stepper_pulleys_belt_5

attach_z_stepper_pulleys_belt_6

1x GT2 timing belt (**O14**) was looped around both timing pulleys and stretched. Before tightning the M3 screws and locking the motor into place, make sure that the belt is not too loose and not too tight. 

attach_z_stepper_pulleys_belt_7

attach_z_stepper_pulleys_belt_8

attach_z_stepper_pulleys_belt_9

attach_z_stepper_pulleys_belt_10

## Stepper motors and end-stops

### Extend stepper motor wires

All 4 stepper motors (2x Y-axis, 1x X-axis and 1x Z-axis) get their power and movement instructions from the Arduino + CNC shield that in a later step will be attached in the small electronic box. Therefore, the stepper motor cables needed to be extended to reach through the cable chains all the way to the front of the machine, where the small electronic box will be located.

AWG22 cables (**E08**) of matching colors were used when increasing the length of the stepper motor cables. The same process was used for all the motors:

1. The amount of wires needed to reach all the way to the electronic box was approximated and cut. Make sure to have an extra ~300 mm wire from the point where the wires exits the Y-axis cable chain, as this will be needed to reach the small electronic box.
2. The ends of the original stepper wires and the extra AWG22 wires were stripped using a wire stripper.
3. The colors of the original stepper wires and the extra AWG22 wires were matched up and the stripped ends of the wires were twisted around each other.
4. The twisted wires where then locked in a steady position by a "third hand".
5. Soldering grease was applied to the twisted wires and the wires were soldered together.
6. 4 shrinking tubes (one per cable) were shrunk around the now soldered twisted wires, covering the soldering.
7. A handful of larger shrinking tubes were shrunk around all 4 wires to keep them together.
8. Finally, the wires were marked using tape and a penn, indicating which stepper motor the wires belonged to. This is important as it will help a lot later on, when the stepper motors are connected to the Arduino.

#### Y-axis 1

The extended wires of the first Y-axis stepper motor were cut at a length so that they reached through the lower front bridge beam (see red arrow on the next image) and through the Y-axis cable chain going to the front of the CNC machine.

solder_steppers_y_axis_1

solder_steppers_y_axis_2

solder_steppers_y_axis_3

solder_steppers_y_axis_4

solder_steppers_y_axis_5

solder_steppers_y_axis_6

solder_steppers_y_axis_7

solder_steppers_y_axis_8

solder_steppers_y_axis_9

solder_steppers_y_axis_10

solder_steppers_y_axis_10_1

#### Y-axis 2

The extended wires of the second Y-axis stepper motor were cut at a length so that they reached through the Y-axis cable chain going to the front of the CNC machine.

solder_steppers_y_axis_11

solder_steppers_y_axis_12

solder_steppers_y_axis_13

solder_steppers_y_axis_14

solder_steppers_y_axis_15

solder_steppers_y_axis_16

solder_steppers_y_axis_17

solder_steppers_y_axis_18

solder_steppers_y_axis_19

solder_steppers_y_axis_20

#### X-axis

I ran out of AWG22 wires when soldering the X-axis stepper motor cables, therefore you will see different type of cables in the upcoming images. Because of this, I had to insert the shrinking tubes before I soldered the cables. Please disregard this and follow the previous instructions.

The extended wire of the X-axis stepper motor were cut at a length so that they reached up and behind the Z-axis stepper motor, through the X-axis cable chain and through the Y-axis cable chain to the front of the CNC machine.

















#### Z-axis

The non-geared NEMA17 motor used for the Z-axis had removable wires, in contrast to the 1:19 geared NEMA17 motors that had non-removable wires. The first step was therefore to connect the wires to the NEMA17 motor and cut of the connector on the other side using a scissor. Otherwise, the same procedure was followed as for the other motors.

The extended wires of the Z-axis stepper motor were cut at a length so that they reached through the X-axis cable chain and through the Y-axis cable chain to the front of the CNC machine.





















### End-stops and end-stop wires

End-stops are important, as they do not only enable you to home the CNC machine, but they also limit the CNC machine from moving past what is physically possible. When the end-stops are triggered, an alarm is fired and the machine automatically stops.

The wires used for end-stops were 0.75 mm^2 (**E03**).

#### X-axis (max)

A microswitch (**E21**) was attached to the thick X-axis (+) end-stop mount (**P10**) using 2x 12mm M3 screws (**S02**).

attach_endstoppers_x_axis_1

attach_endstoppers_x_axis_2

attach_endstoppers_x_axis_3

attach_endstoppers_x_axis_4

The end-stop mount was then pushed against the backside of the top bridge beam, which enabled the end-stop to trigger on the Z-axis stepper motor. The X-axis (carriage) was then moved to its maximum position and the end-stop mount was positioned in a way so that the end-stop triggered just before the X-axis reached its maximum position.

Please ignore the flexible conduit/hose in the next two images, it will be added in an upcoming step.

attach_endstoppers_x_axis_5

attach_endstoppers_x_axis_7

The end-stop mount was then clamped to the upper bridge beam and a small drill (-2 mm) was used to carefully make indentations at the center of the holes. The end-stop mount was then removed. Cutting fluid was applied and a 4 mm drill was used to drill the holes, followed by a M5 drill tap. The end-stop mount was then attached to the upper bridge beam using 2x 40 mm M5 screws (**S13**).

attach_endstoppers_x_axis_8

attach_endstoppers_x_axis_9

attach_endstoppers_x_axis_10

attach_endstoppers_x_axis_11

attach_endstoppers_x_axis_12

attach_endstoppers_x_axis_13

attach_endstoppers_x_axis_14

attach_endstoppers_x_axis_15

attach_endstoppers_x_axis_16

One black and one red 0.75 mm^2 wire (**E03**) were cut out at a length so that they reached from the X-axis max end-stop to the right side plate, through the top bridge beam and through the Y-axis cable chain to the front of the CNC machine. A handful of shrinking tubes (**O24**) were shrunk around the wires to keep them together.

attach_endstoppers_x_axis_17

attach_endstoppers_x_axis_18

attach_endstoppers_x_axis_19

One end of the wires were taped together and inserted through the upper bridge beam to the side plate on the other side.

attach_endstoppers_x_axis_20

attach_endstoppers_x_axis_21

attach_endstoppers_x_axis_22

A flexible conduit/hose (**O13**) was then cut out and the other side of the cables were inserted through the conduit. The flexible conduit was then inserted ~50 mm into the upper bridge beam and the other side was attached to the outside of the upper bridge beam using cable ties (**O11**).

attach_endstoppers_x_axis_23

attach_endstoppers_x_axis_24

attach_endstoppers_x_axis_25

The end of the wires were stripped and twisted. Two 2.8 mm spade connectors (**E25**) were then attached to the stripped wires using a plier. The red wire was then attached to C (Common terminal) pinout on the end-stop and the black cable was connected to the NO (Normally Open) pinout.

attach_endstoppers_x_axis_26

attach_endstoppers_x_axis_27

attach_endstoppers_x_axis_28

attach_endstoppers_x_axis_29

attach_endstoppers_x_axis_30

Finally, the open end of the wires were marked using tape (**O23**) and a penn, indicating which end-stop the cables belonged to. This is important as it will help a lot later on, when the end-stops are connected to the Arduino.

attach_endstoppers_x_axis_31

#### X-axis (min)

A microswitch (**E21**) was attached to the X-axis end-stop (-) mount (**P08**) using 2x 12mm M3 screws (**S02**).

attach_endstoppers_x_axis_32_0

attach_endstoppers_x_axis_32_1

attach_endstoppers_x_axis_32_2

One black and one red 0.75 mm^2 wire (**E03**) were cut out at a length so that they reached from the X-axis end-stop (-), around the left side plate, through the Y-axis cable chain to the front of the CNC machine. A handful of shrinking tubes (**O24**) were shrunk around the wires to keep them together.

attach_endstoppers_x_axis_32

attach_endstoppers_x_axis_33

attach_endstoppers_x_axis_34

The end of the wires were stripped and twisted. Two 2.8 mm spade connectors (**E25**) were then attached to the stripped wires using a plier. The red wire was then attached to C (Common terminal) pinout on the end-stop and the black cable was connected to the NO (Normally Open) pinout.

The wires were initially strapped around the lower front bridge beam (seen in the first two images), but as it turned out it blocked the belt tensioner. So they were instead strapped around the M8 tensioner screw, using a cable tie (**O11**). 

attach_endstoppers_x_axis_36

attach_endstoppers_x_axis_37

attach_endstoppers_x_axis_38

Finally, the open end of the wires were marked using tape and a penn, indicating which end-stop the cables belonged to.

attach_endstoppers_x_axis_39

#### Y-axis (max)

The tall Y-axis end-stop (+) mount (**P09**) was clamped to the inner side of the upper frame and a sharpie was used to indicate the center of the holes. Note that this end-stop mount can probably be redesigned to gain an extra ~10 mm of Y-axis movement, something I will probably do in the future.

attach_endstoppers_y_axis_1

attach_endstoppers_y_axis_2

attach_endstoppers_y_axis_3

attach_endstoppers_y_axis_4

A bradawl and a hammer were then used to make indentations at the center of the holes. Cutting fluid was applied and a 4 mm drill was used to drill the holes, followed by a M5 drill tap. The end-stop mount was then attached to the inside of the upper frame using 2x 20 mm M5 screws (**S12**).

attach_endstoppers_y_axis_5

attach_endstoppers_y_axis_6

attach_endstoppers_y_axis_7

attach_endstoppers_y_axis_8

attach_endstoppers_y_axis_9

attach_endstoppers_y_axis_10

attach_endstoppers_y_axis_11

attach_endstoppers_y_axis_12

One black and one red 0.75 mm^2 wire (**E03**) were cut out at a length so that they reached from the Y-axis end-stop (+) and through the 900 mm aluminium profile of the upper frame to the front of the CNC machine.

attach_endstoppers_y_axis_13

attach_endstoppers_y_axis_14

attach_endstoppers_y_axis_15

A microswitch (**E21**) was attached to the tall Y-axis end-stop (+) mount using 2x 12mm M3 screws (**S02**).

attach_endstoppers_y_axis_17

attach_endstoppers_y_axis_18

attach_endstoppers_y_axis_19

A flexible conduit/hose (**O13**) was then cut out and the wires were inserted through the conduit. The flexible conduit was then inserted ~50 mm into the 900 mm aluminium profile of the upper frame. The other side was bent around and attached to the outside of the upper frame using cable ties (**O11**).

attach_endstoppers_y_axis_20

attach_endstoppers_y_axis_21

attach_endstoppers_y_axis_22

The end of the wires were stripped and twisted. Two 2.8 mm spade connectors (**E25**) were then attached to the stripped wires using a plier. The red wire was then attached to C (Common terminal) pinout on the end-stop and the black cable was connected to the NO (Normally Open) pinout.

attach_endstoppers_y_axis_23

attach_endstoppers_y_axis_24

Finally, the open end of the wires were marked using tape and a penn, indicating which end-stop the cables belonged to.

attach_endstoppers_y_axis_16

#### Y-axis (min)

A microswitch (**E21**) was attached to the Y-axis end-stop (-) mount (**P08**) using 2x 12mm M3 screws (**S02**).

attach_endstoppers_y_axis_25

attach_endstoppers_y_axis_26

attach_endstoppers_y_axis_27

One black and one red 0.75 mm^2 wire (**E03**) were cut out at a length so that they reached from the Y-axis end-stop (-) and to the front of the CNC machine.

The end of the wires were stripped and twisted. Two 2.8 mm spade connectors (**E25**) were then attached to the stripped wires using a plier. The red wire were then attached to C (Common terminal) pinout on the end-stop and the black cable was connected to the NO (Normally Open) pinout.

attach_endstoppers_y_axis_28

attach_endstoppers_y_axis_29

attach_endstoppers_y_axis_30

attach_endstoppers_y_axis_31

A flexible conduit/hose (**O13**) was cut out and the wires were inserted through the conduit. The flexible conduit was attached to the outside of the upper frame using cable ties (**O11**).

attach_endstoppers_y_axis_33

attach_endstoppers_y_axis_34

attach_endstoppers_y_axis_32

attach_endstoppers_y_axis_35

Finally, the open end of the wires were marked using tape and a penn, indicating which end-stop the cables belonged to.

#### Z-axis (max)

The main purpose of the Z-axis end-stop (+) is, apart from homing the machine, to limit the CNC machine from moving past what the length of the rails allow. As the MGN12H blocks contains a lot of small bearing balls, there's a high risk of them falling out if the blocks move past the rail.

To reduce the complexity and amount of wires, I chose not to include a Z-axis end-stop (-), as you are likely to mill straight through your waste board before there's a risk of moving past the Z-axis min limit. But if you want to add a Z-axis min end-stop, just repeat the process in this section with the new switch flipped around.

First, the vertical carriage slider was moved upwards to its maximum point, where the MGN12H blocks are just about to move past the limit of the rails. The Z-axis end-stop trigger (**P39**) was then pressed against the outside of the vertical carriage slider and a sharpie was used to mark the center of the holes.

attach_endstoppers_z_axis_1

attach_endstoppers_z_axis_2

attach_endstoppers_z_axis_3

A 2.5 mm drill was used to drill the holes into the vertical carriage slider. A tip is to mark the drill depth needed using tape. The Z-axis end-stop trigger was then attached to the vertical carriage slider using 2x 12 mm M3 screws (**S02**).

attach_endstoppers_z_axis_4

attach_endstoppers_z_axis_5

attach_endstoppers_z_axis_6

attach_endstoppers_z_axis_7

A microswitch (**E21**) was pressed against the carriage and positioned and aligned to be triggered by the maximum state of the Z-axis end-stop trigger.

attach_endstoppers_z_axis_8

attach_endstoppers_z_axis_9

A 2.5 mm drill was used to drill the first hole into the carriage and the microswitch was attached to the carriage using 1x 12 mm M3 screw (**S02**). After the microswitch was locked into position, the second hole was drilled and the second 12 mm M3 screw (**S02**) was attached.

attach_endstoppers_z_axis_10

attach_endstoppers_z_axis_11

attach_endstoppers_z_axis_12

One black and one red 0.75 mm^2 wire (**E03**) were cut at a length so that they reached over the top bridge beam, through the X-axis cable chain and through the Y-axis cable chain to the front of the CNC machine. A handful of shrinking tubes (**O24**) were shrunk around the wires to keep them together.

attach_endstoppers_z_axis_13

attach_endstoppers_z_axis_14

attach_endstoppers_z_axis_15

The end of the wires were stripped and twisted. Two 2.8 mm spade connectors (**E25**) were then attached to the stripped wires using a plier. The red wire was then attached to C (Common terminal) pinout on the end-stop and the black wire was connected to the NO (Normally Open) pinout.

attach_endstoppers_z_axis_16

attach_endstoppers_z_axis_17

attach_endstoppers_z_axis_18

The wires were strapped around the M8 screw keeping the Z motor mount attached to the carriage, using a cable tie (**O11**).

Finally, the open end of the wires were marked using tape and a penn, indicating which end-stop the cables belonged to.

attach_endstoppers_z_axis_19

attach_endstoppers_z_axis_20

### Stepper motor and end-stop cable management

To keep a nice structure of all the wires, braided cable sleeves (**O08**) and flexible conduits/hoses (**O13**) were used.

#### Y-axis steppers and X-axis end-stops

First, the wires from the right-side Y-axis stepper motor were inserted into a small flexible conduit and pushed through the lower bridge beam closest to the carriage.

stepper_motor_cable_management_1

stepper_motor_cable_management_3

stepper_motor_cable_management_4

The wires from the two geared Y-axis stepper motors and the two X-axis end-stops were bundled together into the same cable sleeve. 

stepper_motor_cable_management_6

stepper_motor_cable_management_6_1

stepper_motor_cable_management_6_2

stepper_motor_cable_management_5

stepper_motor_cable_management_6_3

To simplify pushing the wires and the cable sleeve through the cable chain, the wires were taped together, leaving no loose ends to get stuck in the cable chain. This was needed as the wires were longer than the cable sleeve (to reach all the way to the small electronic box in the front of the CNC machine).

A cable tie (**O11**) was used to close the entrence of the cable sleeve.

stepper_motor_cable_management_6_4

stepper_motor_cable_management_6_5

stepper_motor_cable_management_6_6

#### X-axis stepper, Z-axis stepper and Z-axis end-stop

First, the wires from the X-axis stepper motor were inserted into a flexible conduit (**O13**). The conduit was then bent over the upper bridge beam, strapped to the vaccum mount and Z motor mount, and then pushed behind the Z-axis stepper motor.

stepper_motor_cable_management_9

stepper_motor_cable_management_10

stepper_motor_cable_management_11

stepper_motor_cable_management_12

The wires from the X-axis stepper, Z-axis stepper and the Z-axis end-stop were bundled together into the same cable sleeve. The cable sleeve was cut at a length so that it reached through the X-axis cable chain, around the left side-plate and through the Y-axis cable chain.

To simplify pushing the wires through the cable chains, the wires were taped together, leaving no loose ends to get stuck in the cable chains. This was needed as the wires were longer than the cable sleeve (to reach all the way to the small electronic box in the front of the CNC machine).

A cable tie (**O11**) was used to close the entrence of the cable sock.

stepper_motor_cable_management_13

stepper_motor_cable_management_13_1

stepper_motor_cable_management_13_2

stepper_motor_cable_management_13_3

stepper_motor_cable_management_13_4

stepper_motor_cable_management_13_5

stepper_motor_cable_management_13_6

stepper_motor_cable_management_13_7

stepper_motor_cable_management_13_8

A cable tie (**O11**) was used to strap the cable sleeve to the left side-plate.

stepper_motor_cable_management_13_9

## Router

### Attach router to carriage

A Makita RT0700CJ (**E20**) trimming router was used as I was not able to get my hands on the Makita RT0700C that Ivan is using. To my knowledge, the RT0700CJ is just an upgraded European version of the RT0700C, with the same dimensions.

The trimming router was locked in place by using the router bracket (**P24**), 4x 40mm M5 screws (**S13**), 4x M5 nuts (**N02**) and 4x (10mm x 5mm x 1mm) washers (**W01**).

attach_router_to_carriage_1

attach_router_to_carriage_2

attach_router_to_carriage_3

attach_router_to_carriage_4

attach_router_to_carriage_6

attach_router_to_carriage_7

### Router cable management

**NOTE: THIS PART INCLUDES WIRING OF HIGH VOLTAGE ELECTRICITY THAT CAN BE LETHAL IF NOT DONE PROPERLY. THE COLORS OF THE CABLES CAN VARY DEPENDING ON REGION/COUNTRY AND YOUR COMPONENTS/PINOUT NUMBERS MIGHT LOOK DIFFERENT. BEFORE YOU CONNECT THE POWER CORD TO THE POWER OUTLET, YOU MUST CONSULT WITH A LICENSED ELECTRICIAN TO MAKE SURE THAT EVERYTHING IS PROPERLY WIRED AND THAT IT IS IN LINE WITH YOUR LOCAL LEGISLATIONS.**

To be able to easily replace the trimming router in the future, a power plug (**E04**) and socket were added (**E05**).

router_cable_management_23

First, the router's power cord was cut and stripped at an appropriate length to reach behind the X-axis cable chain mount. A flexible conduit (**O13**) was cut out at an appropriate length and the power cord closest to the router was inserted into the conduit. The end of the power cord and the inside wires were then stripped and twisted.

router_cable_management_1

router_cable_management_2

router_cable_management_3

The power plug was opened up and the wires were connected. The built-in strain relief was then tightened around the cable before the plug was closed again.

router_cable_management_4

router_cable_management_5

router_cable_management_6

router_cable_management_7

router_cable_management_8

The rest of the power cord was inserted through the Y-axis cable chain, around the left side plate (under the cable tie) and through the X-axis cable chain. Getting the power cord through the X-axis cable chain was quite tricky due to the friction of the rubber cable. A cable tie (**O11**) was therefore attached to the top of the cable and used to pull the cable through the cable chain.

router_cable_management_9

router_cable_management_10

router_cable_management_11

router_cable_management_12

router_cable_management_13

router_cable_management_14

router_cable_management_15

The power cord was pulled through the cable chains and adjusted to an appropriate length to reach behind the X-axis cable chain mount. The end of the cable and the inside wires were then stripped and twisted.

router_cable_management_17

router_cable_management_19

The power socket was opened and the wires were attached to the terminals inside. The built-in strain relief was then tightened around the cable before the socket was closed again.

router_cable_management_16

router_cable_management_18

router_cable_management_20

router_cable_management_21

router_cable_management_22

The plug and socket were connected and strapped to the back of the X-axis cable chain mount using cable ties (**O11**). The flexible conduit with the router power cord inside was strapped to the stepper motor flexible conduit using cable ties (**O11**). Make sure that it doesn't touch and drag along the upper bridge beam.

router_cable_management_23

router_cable_management_24

## Electronic boxes

Two electronic boxes were attached to the front side of the CNC machine, a large box to encapsulate the power supply and a small box to encapsulate the Arduino and the CNC shield.

### Small electronic box

The small electronic box consisted of 4 parts (**P02**, **P04**, **P13**, **P15**). The two middle parts were clamped together on the front-left side of the frame, closest to the Y-axis cable chain. A finger was used to feel that the two parts were perfectly lined up.

Make sure to have enought space on the left side of the box for the all the stepper motor wires, end-stop wires and router power cable to enter the box (the vertical beam might block if you attach it too far to the left). Also make sure that the two holes are pointing to the left.

attach_small_electronic_box_1

attach_small_electronic_box_2

attach_small_electronic_box_3

The front-middle part (**P13**) was attached first. A small 2 mm drill was used to make indentations at the center of the holes. Cutting fluid was applied and a 3 mm drill was used to drill the holes, followed by a M4 drill tap. The front-middle and front part was then attached to the frame using 4x 40mm M4 screws (**S11**).

attach_small_electronic_box_4

attach_small_electronic_box_5

attach_small_electronic_box_6

attach_small_electronic_box_7

attach_small_electronic_box_8

attach_small_electronic_box_9

attach_small_electronic_box_10

To attach the back-middle part (**P02**), the whole CNC machine had to be pushed partly over the edge of the working table to be able to drill on the inside of the frame. The machine was firmly clamped to the table.

The back-middle part was again clamped to the frame and aligned with the now attached front-middle part. A small 2 mm drill was used to make indentations at the center of the holes. Cutting fluid was applied and a 3 mm drill was used to drill the holes, followed by a M4 drill tap. The back-middle and back part was then attached to the frame using 4x 25mm M4 screws (**S10**).

attach_small_electronic_box_11

attach_small_electronic_box_12

attach_small_electronic_box_13

attach_small_electronic_box_14

attach_small_electronic_box_15

attach_small_electronic_box_16

### Large electronic box

As the small box, the large electronic box consisted of 4 parts (**P01**, **P03**, **P12**, **P14**). The two middle parts were clamped together to the right of the small box. A finger was used to feel that the two parts were perfectly lined up. 

Make sure that the hole is pointing to the left.

attach_large_electronic_box_1

attach_large_electronic_box_1_1

The front-middle part (**P12**) was attached first. A small 2 mm drill was used to make indentations at the center of the holes. Cutting fluid was applied and a 3 mm drill was used to drill the holes, followed by a M4 drill tap. The front-middle and front part was then attached to the frame using 4x 40mm M4 screws (**S11**).

attach_large_electronic_box_2

attach_large_electronic_box_3

attach_large_electronic_box_4

attach_large_electronic_box_5

attach_large_electronic_box_6

attach_large_electronic_box_7

attach_large_electronic_box_8

To attach the back-middle part (**P01**), the whole CNC machine had to be pushed partly over the edge of the working table to be able to drill on the inside of the frame. The machine was firmly clamped to the table.

The back-middle part was again clamped to the frame and aligned with the now attached front-middle part. A small 2 mm drill was used to make indentations at the center of the holes. Cutting fluid was applied and a 3 mm drill was used to drill the holes, followed by a M4 drill tap. The back-middle and back part was then attached to the frame using 4x 25mm M4 screws (**S10**).

attach_large_electronic_box_9

attach_large_electronic_box_10

attach_large_electronic_box_11

attach_large_electronic_box_12

attach_large_electronic_box_13

attach_large_electronic_box_14

attach_large_electronic_box_15

## Electrical wiring and connect components

### Main power supply

**NOTE: THIS PART INCLUDES WIRING OF HIGH VOLTAGE ELECTRICITY THAT CAN BE LETHAL IF NOT DONE PROPERLY. THE COLORS OF THE CABLES CAN VARY DEPENDING ON REGION/COUNTRY AND YOUR COMPONENTS/PINOUT NUMBERS MIGHT LOOK DIFFERENT. BEFORE YOU CONNECT THE POWER CORD TO THE POWER OUTLET, YOU MUST CONSULT WITH A LICENSED ELECTRICIAN TO MAKE SURE THAT EVERYTHING IS PROPERLY WIRED AND THAT IT IS IN LINE WITH YOUR LOCAL LEGISLATIONS.**

The large electronic box was detached from the frame.

The 200W power supply (**E02**) was then attached to the back panel of the larger electronic box using 4x 5mm M3 screws (**S07**) unscrewed from the geared stepper motors.

connect_main_electronic_box_1

connect_main_electronic_box_2

connect_main_electronic_box_3

The C14 connector/terminal (**E14**) and the emergency stop switch (**E17**) were inserted into the holes on the front plate of the large electronic box. 

connect_main_electronic_box_4

connect_main_electronic_box_5

connect_main_electronic_box_6

A small brown/red wire (**E06**) was cut out and the ends were stripped and twisted. Two 4.8 mm spade connectors (**E26**) were then attached to the stripped wire using a plier. The space connectors were connected between **10** and **1A** on the back side of the C14 connector.

connect_main_electronic_box_7

connect_main_electronic_box_8

connect_main_electronic_box_9

connect_main_electronic_box_10

A longer brown wire was cut out to reach between **L** on the C14 connector and **13** on the emergency stop switch. The ends were stripped and twisted. A 4.8 mm spade connector (**E26**) was attached to the side connected to the C14 connector and a 6.3 mm space connector (**E27**) was attached to the side connected to the emergency stop switch. The spade connectors were then connected.

connect_main_electronic_box_11

connect_main_electronic_box_12

connect_main_electronic_box_13

Two short and one longer blue wire were cut out at an appropriate length and the ends of the wires were stripped and twisted.

connect_main_electronic_box_14

Two 4.8 mm spade connector (**E26**) were attached to one of the sides of each shorter wire and the other sides were inserted and locked into 1x 3-way Wago 221-413 (**E07**).

connect_main_electronic_box_15

connect_main_electronic_box_16

A 6.3 mm space connector (**E27**) was attached to one side of the longer blue wire and the other side were inserted and locked into the 3-way Wago 221-413 (**E07**).

I didn't have access to matching colors of all the spade connectors, so I followed the appropriate color scheme of the wires instead. So please ignore if there's a mismatch between the wire color and the spade connector color in the upcoming images.

connect_main_electronic_box_17

The shorter blue wires were connected to **N** and **XX** on the C14 connector. The longer blue wire was connected to **23** on the emergency stop switch.

connect_main_electronic_box_18

connect_main_electronic_box_19

One brown and one blue wire were cut out to reach between the emergency stop switch and the power supply's input terminals. The ends of the wires were stripped and twisted. Two 6.3 mm space connectors (**E27**) were attached to one side of the wires and 2x M4 ring terminals (**E24**) were attached to the other side. The blue wire's spade connector was connected to **24** on the emergency stop switch. The brown wire's spade connector was connected to **14** on the emergency stop switch.

connect_main_electronic_box_20

connect_main_electronic_box_21

connect_main_electronic_box_22

A small green/yellow wire was cut out to reach between the C14 connector and the power supply's input terminals. The end of the wire was stripped and twisted, a 4.8 mm spade connector (**E26**) was attached to one side and 1x M4 ring terminal (**E24**) was attached to the other side. The spade connector was then attached to **⏚** (ground) on the C14 connector.

connect_main_electronic_box_23

connect_main_electronic_box_24

The three M4 ring terminals were then connected to the power supply's input terminals in the following way:

* Brown -> AC/L
* Blue -> AC/N
* Green/Yellow -> **⏚** (ground)

connect_main_electronic_box_25

connect_main_electronic_box_26

Power was connected to the C14 connector (read [this](#connect-main-electronic-box) note before connecting the power) and a multimeter was used to verify that the power supply outputted 12V. The multimeter was also used to verify that the C14 connector worked properly (cut power when using the switch) and that the emergency stop switch worked propertly (cut power when pushed. Also that the emegency stop switch remains off when C14 connector is switched off and on again).

connect_main_electronic_box_26

The emergency stop switch was attached to the front plate using 2x 18mm M4 screws (**S09**), 2x M4 nuts (**N01**) and two (9 mm, 4.5 mm, 1 mm) washers (**W07**).

connect_main_electronic_box_27

connect_main_electronic_box_28

The C14 connector was attached to the front plate using super glue. A cloth was used to remove excess glue.

connect_main_electronic_box_28_1

connect_main_electronic_box_28_2

connect_main_electronic_box_28_3

Shrink tubes (**O24**) were cut out at an appropriate length, one for each spade connector. Each spade connector was then temporarily removed and inserted into its shrink tube, before attached back again. The shrink tubes were then shrunk around all the spade connectors.

connect_main_electronic_box_29

connect_main_electronic_box_30

connect_main_electronic_box_31

connect_main_electronic_box_32

### Prepare power to steppers and connect fans and LED

To prepare the power for the stepper motors, one black and one red wire (**E03**) were cut out (approx. 300 mm long) to reach between the 12V terminals on the power supply and the small electronic box containing the Arduino and CNC shield. One side of each wire was then stripped and twisted, and 2x M3 ring terminals (**E23**) were attached. 

The red wire was connected to the **V+** and the black wire was connected to **V-**.

connect_main_electronic_box_33

connect_main_electronic_box_34

connect_main_electronic_box_35

A 40x40 mm 12V fan (**E01**) was attached to the back side of the large electronic box's front panel, using 4x 12 mm M3 screws (**S02**). The fan was attached to blow air out of the box.

attach_fans_led_1

attach_fans_led_2

attach_fans_led_3

A 12V red LED (**E22**) was inserted into the small 
~8 mm hole on the front of the large electronic box's front panel.

attach_fans_led_4

attach_fans_led_5

attach_fans_led_6

The second 40x40 mm 12V fan (**E01**) was attached to the back side of the small electronic box's front panel, using 4x 12 mm M3 screws (**S02**). A short flexible conduit (**O13**) reaching between the two eletronic boxes was cut out and the wires from the fan were inserted through it.

attach_fans_led_7

attach_fans_led_8

attach_fans_led_9

attach_fans_led_9

The loose wires of the two fans and the LED were stripped and twisted together, black together and red together. Then all three black wires were attached into the same M3 ring terminal (**E23**) and all three red wires were attached into the same M3 ring terminal (**E23**).

attach_fans_led_10

attach_fans_led_11

attach_fans_led_11

The red wires (red ring terminal) were finally connected to the **V+** and the black wires (blue ring terminal) were connected to **V-** on the 12V power supply.

attach_fans_led_13

The red and black 12V power wires intended for the stepper motors were inserted through the same short flexible conduit as the fan wires.

attach_fans_led_14

2x 3d-printed strain relief halves (**P11**) were inserted into the hole on the side of the large electronic box facing the small electronic box. The large box was then carefully closed and attached to the upper and lower frame again. It's really important that you don't have to force it closed. If that's the case you need to move some cables for it to close smoothly.

attach_fans_led_15

attach_fans_led_16

attach_fans_led_17

attach_fans_led_18

### Assemble stepper motor drivers and tune VRef

One small heatsink was attached to each DRV8825 stepper driver (**E16**).

vref_stepper_drivers_1

vref_stepper_drivers_2

Before the stepper motors were connected to the CNC shield, the stepper motor drivers' VRef needed to be tuned. The VRef regulates the voltage from the stepper driver to the stepper motor. If the VRefs are set to high, it can damage the stepper motors by supplying to much voltage.

The CNC shield (**E10**) was first attached to the Arduino Uno (**E09**).

vref_stepper_drivers_3

vref_stepper_drivers_4

The four stepper drivers were then attached to the CNC shield, one for each axis (X, Y, Z) and one for the mirrored Y-axis (A). The stepper drivers were inserted so that the "EN" pins on the stepper drivers aligned with the EN female terminal on the CNC shield.

vref_stepper_drivers_5

vref_stepper_drivers_6

vref_stepper_drivers_7

A USB cable (**E28**) was connected to the Arduino Uno and to a computer to supply the Arduino with power. 

The power wires connected to the 12v power supply were connected to the CNC shield:

* Red cable -> **+**
* Black cable -> **-**

Power was then added to the system by inserting the C13 cable (**E30**) into the C14 connector on the front panel of the large electronic box.

vref_stepper_drivers_8

A multimeter was then used to regulate the VRef on each stepper driver. The equation to calculate the VRef differs depending on the stepper driver. The DRV8825 stepper drivers are using the following equation:

vref_stepper_drivers_8_1

By checking the `I_{max}` in the technical specification for each stepper motor, the following VRefs were calculated for each stepper driver:

| Stepper driver  | I_{max} | VRef |
|---|---|---|
| X | 1.68A | 1.68/2 = 0.84V |
| Y | 1.68A | 1.68/2 = 0.84V |
| A (mirrored Y)  | 1.68A | 1.68/2 = 0.84V |
| Z | 1.68A | 1.68/2 = 0.84V |

To measure the VRef of each stepper driver, the red test probe was connected to the screw on top of the stepper driver, and the black test probe was connected to the second bottom left pin (GND). The screw was then rotated to adjust the VRef to the appropriate voltage (~0.84V).

vref_stepper_drivers_9

vref_stepper_drivers_10

### Attach Arduino and solder USB cable

The CNC shield was removed from the Arduino and the Arduino was attached to the back plate of the small electronic box using the 4x 5mm M3 screws (**S07**) unscrewed from the geared stepper motors. The USB cable was left inserted in the Arduino, as there was no space to insert it afterwards.

arduino_and_usb_1

arduino_and_usb_2

arduino_and_usb_3

The end of the USB cable was cut and stripped, showing the following 4 wires inside:

| Color | Type |
|---|---|
| Red | VCC (+5V) |
| White | Data - |
| Green | Data + |
| Black | GND |

Each wire was stripped and twisted.

arduino_and_usb_3_1

A female USB-A (**E29**) was inserted into the front plate of the small electronic box. By using a soldering iron, solder/filler metal was first added to each pin on the female USB-A before attaching the wires, to simplify the soldering. 

arduino_and_usb_4

arduino_and_usb_4

4 small shrink tubes (**O24**) were cut out and the wires were inserted into the shrink tubes. 

arduino_and_usb_7

arduino_and_usb_8

To know which wire to solder to which pin, the following schema was used. The schema illustrates when looking straight into the female USB-A, with the flat surface at the top and the internal USB pins pointing downwards. As the pins goes straight through the connector, it's possible to map it to the pins on the back.

arduino_and_usb_6_1

arduino_and_usb_6

When the correct pin-wire-mapping was found, the wires were soldered one by one, by placing the stripped wires on the pins and then pressing the solder iron onto the tip of the wires. As filler metal had already been applied to the pins, no extra filler metal had to be added. The shrink tubes were then shrunk around the wires.

arduino_and_usb_9

arduino_and_usb_10

Finally, a 3d-printed block (**P33**) was glued to the female USB-A connector and the back of the front panel to lock it into place.

arduino_and_usb_11

arduino_and_usb_12

arduino_and_usb_13

arduino_and_usb_14

### Stepper and end-stop cable management to small electronic box

The CNC shield was attached to the Arduino and 6x 3d-printed strain relief halves (**P11**) were inserted into the holes on the sides of the small electronic box.

steppers_to_cnc_shield_1

steppers_to_cnc_shield_2

Two flexible conduits (**O13**) were cut out to reach between the end of the Y-axis cable chain and the two holes in the small box. A hole was then drilled in the upper flexible conduit for the Y-axis end-stop wires to enter. To do this, the upper flexible conduit was placed where it was intended to be and tape was used to indicate the position of the hole. 

A drill was then used to create the hole in the upper flexible conduit.

steppers_to_cnc_shield_3

steppers_to_cnc_shield_4

steppers_to_cnc_shield_5

steppers_to_cnc_shield_6

The Y-axis end-stop (+ and -) wires were inserted into the hole, followed by half of the wires coming from the Y-axis cable chain. The rest of the wires were inserted into the lower flexible conduit.

To simplify the process, the cables going into the same conduit were taped together.

steppers_to_cnc_shield_7

steppers_to_cnc_shield_8

steppers_to_cnc_shield_9

The end of the conduits were then placed between the strain relief halves and the front-middle part of the box were carefully attached to the frame again, locking the strain reliefs and the flexible conduits in place.

steppers_to_cnc_shield_10

steppers_to_cnc_shield_11

### Connect steppers to CNC shield

To keep a good structure of the wires inside the small box, electrical crimp sleeves (**E15**) and contact housings (**E13**) were used. This also reduced the risks of shortings and loose wires.

steppers_to_cnc_shield_13

steppers_to_cnc_shield_18

For each stepper, the wires were cut at an appropriate length to reach to its connection on the CNC shield. Each wire were stripped and twisted. An AWG22/24 crimp connector was then attached to the end of each wire using a crimping tool. A shrinking tube (**O24**) was shrunk around the wires to keep a good structure.

The wires were then inserted and locked into a 1X4 contact housing (**E13**). Make sure to insert the wires in the correct orinentation, as the crimp connector has a "lock" that interlocks with the contact housing.

To know in which order to insert the wires, check the technical specification of your steppers. You should find something like this (given that you've bought bi-polar stepper motors):

| A+ | A- | B+  | B- |
|---|---|-----|---|
| Black | Green | Red | Blue |

**A** and **B** indicate the two different coils in the stepper motor and the colors are the colors of the wires. You want to connect the crimp connectors so that each coil's wires are next to each other: **A A B B**.

steppers_to_cnc_shield_12

steppers_to_cnc_shield_14

steppers_to_cnc_shield_15

steppers_to_cnc_shield_16

steppers_to_cnc_shield_17

steppers_to_cnc_shield_19

This was done for all four steppers (X, Y, Z, A (mirrored Y)). Tape and a sharpie was used to indicate which contact housing beloning to which stepper. The contact housings were then connected to its connections on the CNC shield.

Note that if any of the steppers are moving in the "wrong" direction later on, you can just turn the connection 180 degrees and it will move the opposite way.

steppers_to_cnc_shield_20

steppers_to_cnc_shield_21

Finally, two jumpers (**E19**) were attached to the blue and yellow column on the "Y row". This tells the Arduino to mirror the Y-stepper instructions to the stepper connected to the **A** connection.

steppers_to_cnc_shield_22

steppers_to_cnc_shield_23

### Connect end-stops to CNC shield

As with the stepper motor wires, electrical crimp connectors were used to keep a good structure in the small electornic box.

For each end-stop, the two wires were cut at an appropriate length to reach to its connection on the CNC shield. Each wire were stripped and twisted. An AWG22/24 crimp connector (**E15**) was then attached to the end of each wire using a crimping tool. 

endstops_to_cnc_shield_1

endstops_to_cnc_shield_2

As I didn't have access to any 1x2 contact housings (**E12**), a shrinking tube (**O24**) was shrunk around each crimp connectors to reduce the risk of shorts.

This was done for all end-stops (X+, X-, Y+, Y- and Z+). Tape and a sharpie was used to indicate which pair of wires beloning to which end-stop. The crimp connector pairs were then connected to its connections on the CNC shield.

endstops_to_cnc_shield_3

endstops_to_cnc_shield_4

endstops_to_cnc_shield_5

endstops_to_cnc_shield_6

### Set microstepping

Microstepping is a way to control the stepper motors in a smoother way and at a higher resolution, but usually at a lower speed and torque. 

The 6 pins (M0, M1, M2) underneath each stepper driver were used to set the microstepping for each motor. By shorting the pins in certain combinations, different type of microstepping can be achieved (**0** indicates no shorting, **1** indicates shorting):

| Microstepping | M0 | M1 | M2 |
|---|----|----|----|
| Full-step | 0  | 0  | 0  |
| 1/2 | 1  | 0  | 0  |
| 1/4 | 0  | 1  | 0  |
| 1/8 | 1  | 1  | 0  |
| 1/16 | 0  | 0  | 1  |
| 1/32 | 1  | 0  | 1  |

The 4 stepper drivers were carefully removed. The microstepping was set to `1/16` for each motor by shorting the two `M2` pins using jumpers (**E19**). The stepper drivers were then carefully inserted back again.

set_microstepping_1

set_microstepping_2

### Router cable management and connect to main power supply

**NOTE: THIS PART INCLUDES WIRING OF HIGH VOLTAGE ELECTRICITY THAT CAN BE LETHAL IF NOT DONE PROPERLY. THE COLORS OF THE CABLES CAN VARY DEPENDING ON REGION/COUNTRY AND YOUR COMPONENTS/PINOUT NUMBERS MIGHT LOOK DIFFERENT. BEFORE YOU CONNECT THE POWER CORD TO THE POWER OUTLET, YOU MUST CONSULT WITH A LICENSED ELECTRICIAN TO MAKE SURE THAT EVERYTHING IS PROPERLY WIRED AND THAT IT IS IN LINE WITH YOUR LOCAL LEGISLATIONS.**

As I wanted the emergency stop switch to kill the router as well, the router cable was inserted into the small electronic box to reach the emergency stop switch in the large electronic box.

A round cable grommet (**O25**) was inserted in the left side of the small electronic box, aligned between the two main wire holes.

The center of the hole was measured and drilled using a 8.5 mm drill. The cable grommet was then inserted and super glue was used to keep it in place.

router_small_box_1

router_small_box_2

router_small_box_3

router_small_box_4

router_small_box_5

The router cable was then inserted into the cable grommet. Some ordinary soap was used to reduce the friction between the rubber cable grommet and the rubber cable.

A cable tie (**O11**) was closed around the router cable on the inside of the box as a strain relief.

router_small_box_6

router_small_box_7

router_small_box_6_1

The large electronic box was opened once more and the router cable was inserted through the flexible conduit into the large electronic box. A cable clip (**O10**) was then used to position the router cable inside the small box.

The small electronic box was then carefully closed. It's really important that you don't have to force it closed. If that's the case you need to move some cables for it to close smoothly.

router_small_box_8

router_small_box_9

router_small_box_10

router_small_box_11

The blue and brown wires going between the emergency stop switch and the 12V power supply were cut in the middle and stripped and twisted. The router cable and the wires inside were also stripped and twisted.

router_small_box_12

router_small_box_14

router_small_box_15

router_small_box_13

The three brown wires were inserted and locked into a 3-way Wago 221-413 (**E07**). The three blue wires were also inserted and locked into a 3-way Wago 221-413 (**E07**).

The large electronic box was then carefully closed once more. It's really important that you don't have to force it closed. If that's the case you need to move some cables for it to close smoothly.

router_small_box_16

router_small_box_17

router_small_box_18

### Final test of electrical wiring

The electrical wiring was tested by plugging in a C13 cable (**E30**) into the C14 socket and the C14 switch and emergency stop switch were turned on. But before this was done, I made sure that the router was turned off.

The red LED should light up, both fans should rotate and the router should rotate when turned on.

test_electrical_wiring_1

test_electrical_wiring_2

test_electrical_wiring_3

test_electrical_wiring_4

test_electrical_wiring_5

## Wasteboard

### Cut out wasteboard

The length and width of the CNC was measured and a 12 mm plywood (**O26**) was cut out using a vertical panel saw. If you don't have a vertical panel saw, a jigsaw or a circular saw works as well.

wasteboard_1

wasteboard_2

wasteboard_3

### Attach wasteboard to CNC

The wasteboard was placed underneath the CNC machine. 7x 3d-printed wasteboard brackets (**P37**), 14x 3.5x20mm screws (**S01**) and 14x (15mm x 5mm x 1mm) washers (**W02**) were used to to keep the wasteboard in place.

wasteboard_4

wasteboard_5

wasteboard_7

wasteboard_6

wasteboard_8

wasteboard_9
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

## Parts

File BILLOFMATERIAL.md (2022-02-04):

# Bill of materials

This page includes an aggregated overview (incl. images) of all the parts needed to build the CNC-machine. To get a better understanding of how the parts are used (additional comments etc), check the following detailed spreadsheet:

* [On Google drive](https://docs.google.com/spreadsheets/d/1VdnPilA22OfAh9a1y4Ft6c2xkio206Dzv85h7AX7CmQ/edit?usp=sharing)
* [Bill\_of\_material.xlsx](./Bill_of_material.xlsx)

The 3d-printed parts were printed in standard PLA using:

* 30% infill
* 4 top solid horizontal layers
* 4 bottom solid horizontal layers
* 4 perimeters

The complete PrusaSlicer config used can be found here: [prusa\_slicer\_config.ini](./prusa_slicer_config.ini)

## 3d-printed parts

| Item No. | Type | Amount | Image | STL-file | OBJ-file |
|---|---|---|---|---|---|
| P01 | Back middle panel (large electronic box)  | 1 | Missing | [middle\_back\_panel\_electronic\_box\_large.stl](./stl_files/electronic_box_large/middle_back_panel_electronic_box_large.stl) | [middle\_back\_panel\_electronic\_box\_large.obj](./obj_files/electronic_box_large/middle_back_panel_electronic_box_large.obj) |
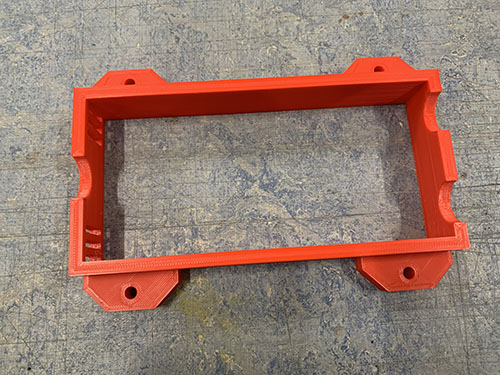
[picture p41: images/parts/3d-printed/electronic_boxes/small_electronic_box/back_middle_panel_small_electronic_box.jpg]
back_middle_panel_small_electronic_box
| P02 | Back middle panel (small electronic box)  | 1 |  | [middle\_back\_panel\_electronic\_box\_small.stl](./stl_files/electronic_box_small/middle_back_panel_electronic_box_small.stl) | [middle\_back\_panel\_electronic\_box\_small.obj](./obj_files/electronic_box_small/middle_back_panel_electronic_box_small.obj) |
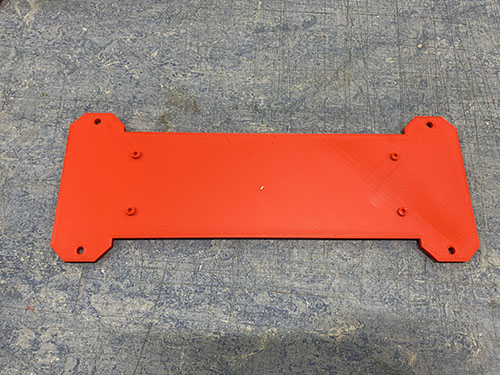
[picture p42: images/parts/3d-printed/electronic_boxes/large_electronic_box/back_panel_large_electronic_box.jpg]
back_panel_large_electronic_box
| P03 | Back panel (large electronic box) | 1 |  | [back\_panel\_electronic\_box\_large.stl](./stl_files/electronic_box_large/back_panel_electronic_box_large.stl) | [back\_panel\_electronic\_box\_large.obj](./obj_files/electronic_box_large/back_panel_electronic_box_large.obj) |
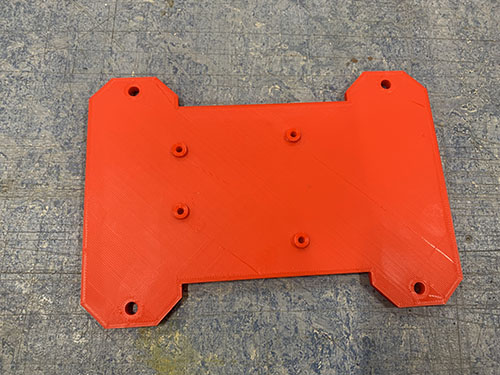
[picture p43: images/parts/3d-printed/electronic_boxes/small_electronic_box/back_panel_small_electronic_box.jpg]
back_panel_small_electronic_box
| P04 | Back panel (small electronic box) | 1 |  | [back\_panel\_electronic\_box\_small.stl](./stl_files/electronic_box_small/back_panel_electronic_box_small.stl) | [back\_panel\_electronic\_box\_small.obj](./obj_files/electronic_box_small/back_panel_electronic_box_small.obj) |
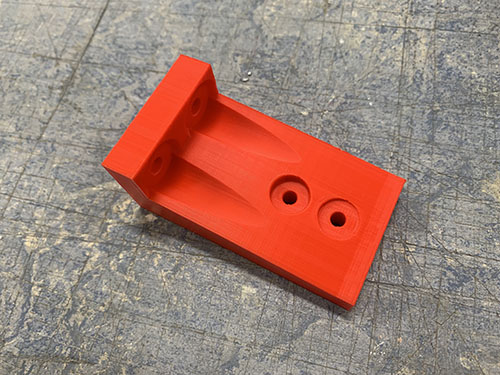
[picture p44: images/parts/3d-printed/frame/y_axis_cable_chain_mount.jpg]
y_axis_cable_chain_mount
| P05 | Cable chain mount | 1 |  | [Y\_CHAIN\_BOTTOM\_BRACKET\_SUPPORT\_1.stl](./stl_files/other/Y_CHAIN_BOTTOM_BRACKET_SUPPORT_1.stl) | [Y\_CHAIN\_BOTTOM\_BRACKET\_SUPPORT\_1.obj](./obj_files/other/Y_CHAIN_BOTTOM_BRACKET_SUPPORT_1.obj) |
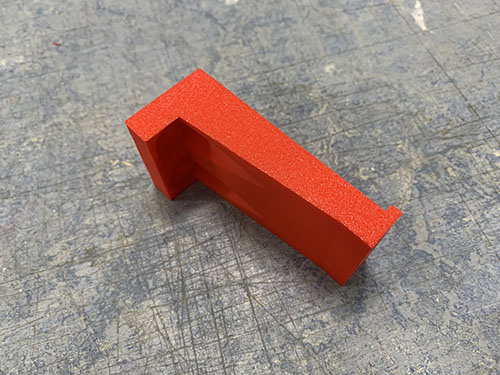
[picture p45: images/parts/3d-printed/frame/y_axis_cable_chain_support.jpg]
y_axis_cable_chain_support
| P06 | Cable chain support | 1 |  | [Y\_CHAIN\_BOTTOM\_BRACKET\_SUPPORT\_2.stl](./stl_files/other/Y_CHAIN_BOTTOM_BRACKET_SUPPORT_2.stl) | [Y\_CHAIN\_BOTTOM\_BRACKET\_SUPPORT\_2.obj](./obj_files/other/Y_CHAIN_BOTTOM_BRACKET_SUPPORT_2.obj) |
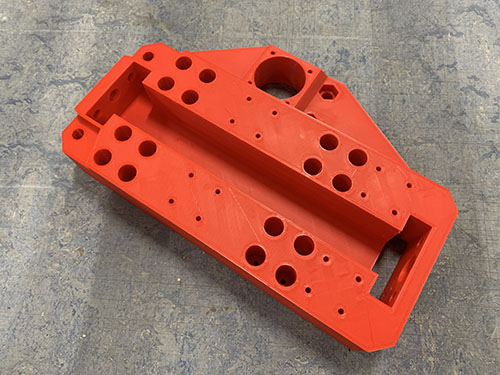
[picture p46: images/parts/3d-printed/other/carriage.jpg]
carriage
| P07 | Carriage | 1 |  | [CARRIAGE.stl](./stl_files/router/CARRIAGE.stl) | [CARRIAGE.obj](./obj_files/router/CARRIAGE.obj) |
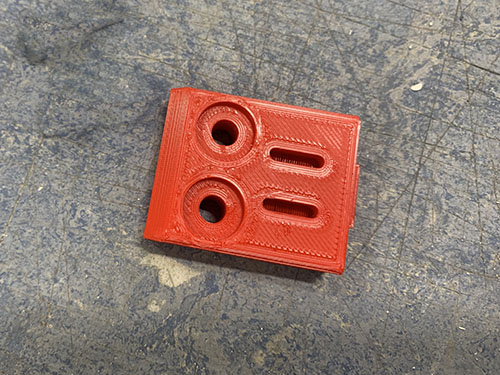
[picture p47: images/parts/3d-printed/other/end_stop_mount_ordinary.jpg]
end_stop_mount_ordinary
| P08 | End-stop mount (ordinary) | 3 |  | [ENDSTOP\_LIMIT\_SWITCH.stl](./stl_files/other/ENDSTOP_LIMIT_SWITCH.stl) | [ENDSTOP\_LIMIT\_SWITCH.obj](./obj_files/other/ENDSTOP_LIMIT_SWITCH.obj) |
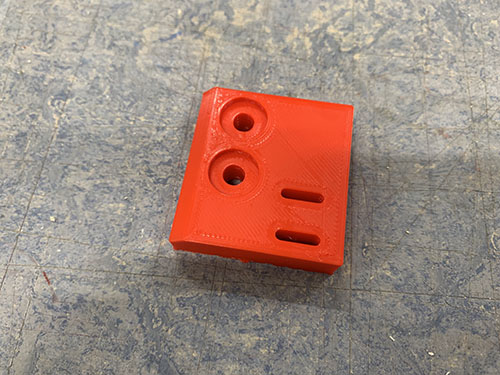
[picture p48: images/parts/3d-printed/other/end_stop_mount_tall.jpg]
end_stop_mount_tall
| P09 | End-stop mount (tall) | 1 |  | [Y\_AXIS\_ENDSTOP\_LIMIT\_SWITCH\_LONG.stl](./stl_files/other/Y_AXIS_ENDSTOP_LIMIT_SWITCH_LONG.stl) | [Y\_AXIS\_ENDSTOP\_LIMIT\_SWITCH\_LONG.obj](./obj_files/other/Y_AXIS_ENDSTOP_LIMIT_SWITCH_LONG.obj) |
| P10 | End-stop mount (thick) | 1 | end_stop_mount_thick | [X\_AXIS\_ENDSTOP\_LIMIT\_SWITCH\_THICK.stl](./stl_files/other/X_AXIS_ENDSTOP_LIMIT_SWITCH_THICK.stl) | [X\_AXIS\_ENDSTOP\_LIMIT\_SWITCH\_THICK.obj](./obj_files/other/X_AXIS_ENDSTOP_LIMIT_SWITCH_THICK.obj) |
| P11 | Flexible conduit strain relief (halves) | 8 | cable_strain_relief | [CABLE\_STRAIN\_RELIEF.stl](./stl_files/other/CABLE_STRAIN_RELIEF.stl) | [CABLE\_STRAIN\_RELIEF.obj](./obj_files/other/CABLE_STRAIN_RELIEF.obj) |
| P12 | Front middle panel (large electronic box) | 1 | front_middle_panel_large_electronic_box | [middle\_front\_panel\_electronic\_box\_large.stl](./stl_files/electronic_box_large/middle_front_panel_electronic_box_large.stl) | [middle\_front\_panel\_electronic\_box\_large.obj](./obj_files/electronic_box_large/middle_front_panel_electronic_box_large.obj) |
| P13 | Front middle panel (small electronic box) | 1 | front_middle_panel_small_electronic_box | [middle\_front\_panel\_electronic\_box\_small.stl](./stl_files/electronic_box_small/middle_front_panel_electronic_box_small.stl) | [middle\_front\_panel\_electronic\_box\_small.obj](./obj_files/electronic_box_small/middle_front_panel_electronic_box_small.obj) |
| P14 | Front panel (large electronic box) | 1 | front_panel_large_electronic_box | [front\_panel\_electronic\_box\_large.stl](./stl_files/electronic_box_large/front_panel_electronic_box_large.stl) | [front\_panel\_electronic\_box\_large.obj](./obj_files/electronic_box_large/front_panel_electronic_box_large.obj) |
| P15 | Front panel (small electronic box) | 1 | front_panel_small_electronic_box | [front\_panel\_electronic\_box\_small.stl](./stl_files/electronic_box_small/front_panel_electronic_box_small.stl) | [front\_panel\_electronic\_box\_small.obj](./obj_files/electronic_box_small/front_panel_electronic_box_small.obj) |
| P16 | Idler block | 3 | idler_block | [IDLER\_BLOCK.stl](./stl_files/other/IDLER_BLOCK.stl) | [IDLER\_BLOCK.obj](./obj_files/other/IDLER_BLOCK.obj) |
| P17 | Left belt tension slider | 1 | y-axis_left_belt_tension_slider | [Y\_AXIS\_LEFT\_BELT\_TENSIONER.stl](./stl_files/belt_tensioner/y_axis_left/Y_AXIS_LEFT_BELT_TENSIONER.stl) | [Y\_AXIS\_LEFT\_BELT\_TENSIONER.obj](./obj_files/belt_tensioner/y_axis_left/Y_AXIS_LEFT_BELT_TENSIONER.obj) |
| P18 | Left belt tensioner | 1 | y-axis_left_belt_tension | [Y\_AXIS\_LEFT\_FRONT\_CLIP.stl](./stl_files/belt_tensioner/y_axis_left/Y_AXIS_LEFT_FRONT_CLIP.stl) | [Y\_AXIS\_LEFT\_FRONT\_CLIP.obj](./obj_files/belt_tensioner/y_axis_left/Y_AXIS_LEFT_FRONT_CLIP.obj) |
| P19 | Left fixed belt tensioner | 1 | y-axis_left_fixed_belt_tension | [Y\_AXIS\_LEFT\_BACK\_CLIP.stl](./stl_files/belt_tensioner/y_axis_left/Y_AXIS_LEFT_BACK_CLIP.stl) | [Y\_AXIS\_LEFT\_BACK\_CLIP.obj](./obj_files/belt_tensioner/y_axis_left/Y_AXIS_LEFT_BACK_CLIP.obj) |
| P20 | Left side plate | 1 | left_plate | [LEFT\_PLATE.stl](./stl_files/side_plates/left/LEFT_PLATE.stl) | [LEFT\_PLATE.obj](./obj_files/side_plates/left/LEFT_PLATE.obj) |
| P21 | Left side plate lower back clip | 1 | left_side_plate_lower_back_clip | [LEFT\_PLATE\_BACK\_CLIP.stl](./stl_files/side_plates/left/LEFT_PLATE_BACK_CLIP.stl) | [LEFT\_PLATE\_BACK\_CLIP.obj](./obj_files/side_plates/left/LEFT_PLATE_BACK_CLIP.obj) |
| P22 | Left side plate lower front clip | 1 | left_side_plate_lower_front_clip | [LEFT\_PLATE\_LOWER\_FRONT\_CLIP.stl](./stl_files/side_plates/left/LEFT_PLATE_LOWER_FRONT_CLIP.stl) | [LEFT\_PLATE\_LOWER\_FRONT\_CLIP.obj](./obj_files/side_plates/left/LEFT_PLATE_LOWER_FRONT_CLIP.obj) |
| P23 | Left side plate upper front clip | 1 | left_side_plate_upper_front_clip | [LEFT\_PLATE\_UPPER\_FRONT\_CLIP.stl](./stl_files/side_plates/left/LEFT_PLATE_UPPER_FRONT_CLIP.stl) | [LEFT\_PLATE\_UPPER\_FRONT\_CLIP.obj](./obj_files/side_plates/left/LEFT_PLATE_UPPER_FRONT_CLIP.obj) |
| P24 | Milling router bracket | 1 | router_bracket | [ROUTER\_BRACKET.stl](./stl_files/router/ROUTER_BRACKET.stl) | [ROUTER\_BRACKET.obj](./obj_files/router/ROUTER_BRACKET.obj) |
| P25 | Rail support | 3 | rails_support | [RAILS\_SUPPORT.stl](./stl_files/other/RAILS_SUPPORT.stl) | [RAILS\_SUPPORT.obj](./obj_files/other/RAILS_SUPPORT.obj) |
| P26 | Right belt tension slider | 1 | y-axis_right_belt_tension_slider | [Y\_AXIS\_RIGHT\_BELT\_TENSIONER.stl](./stl_files/belt_tensioner/y_axis_right/Y_AXIS_RIGHT_BELT_TENSIONER.stl) | [Y\_AXIS\_RIGHT\_BELT\_TENSIONER.obj](./obj_files/belt_tensioner/y_axis_right/Y_AXIS_RIGHT_BELT_TENSIONER.obj) |
| P27 | Right belt tensioner | 2 | y-axis_right_belt_tension | [Y\_AXIS\_RIGHT\_FRONT\_CLIP.stl](./stl_files/belt_tensioner/y_axis_right/Y_AXIS_RIGHT_FRONT_CLIP.stl) | [Y\_AXIS\_RIGHT\_FRONT\_CLIP.obj](./obj_files/belt_tensioner/y_axis_right/Y_AXIS_RIGHT_FRONT_CLIP.obj) |
| P28 | Right fixed belt tensioner | 2 | y-axis_right_fixed_belt_tension | [Y\_AXIS\_RIGHT\_BACK\_CLIP.stl](./stl_files/belt_tensioner/y_axis_right/Y_AXIS_RIGHT_BACK_CLIP.stl) | [Y\_AXIS\_RIGHT\_BACK\_CLIP.obj](./obj_files/belt_tensioner/y_axis_right/Y_AXIS_RIGHT_BACK_CLIP.obj) |
| P29 | Right side plate | 1 | right_plate | [RIGHT\_PLATE.stl](./stl_files/side_plates/right/RIGHT_PLATE.stl) | [RIGHT\_PLATE.obj](./obj_files/side_plates/right/RIGHT_PLATE.obj) |
| P30 | Right side plate lower back clip | 1 | right_side_plate_lower_back_clip | [RIGHT\_PLATE\_BACK\_CLIP.stl](./stl_files/side_plates/right/RIGHT_PLATE_BACK_CLIP.stl) | [RIGHT\_PLATE\_BACK\_CLIP.obj](./obj_files/side_plates/right/RIGHT_PLATE_BACK_CLIP.obj) |
| P31 | Right side plate lower front clip | 1 | right_side_plate_lower_front_clip | [RIGHT\_PLATE\_LOWER\_FRONT\_CLIP.stl](./stl_files/side_plates/right/RIGHT_PLATE_LOWER_FRONT_CLIP.stl) | [RIGHT\_PLATE\_LOWER\_FRONT\_CLIP.obj](./obj_files/side_plates/right/RIGHT_PLATE_LOWER_FRONT_CLIP.obj) |
| P32 | Right side plate upper front clip | 1 | right_side_plate_upper_front_clip | [RIGHT\_PLATE\_UPPER\_FRONT\_CLIP.stl](./stl_files/side_plates/right/RIGHT_PLATE_UPPER_FRONT_CLIP.stl) | [RIGHT\_PLATE\_UPPER\_FRONT\_CLIP.obj](./obj_files/side_plates/right/RIGHT_PLATE_UPPER_FRONT_CLIP.obj) |
| P33 | USB lock | 1 | USB_A_female | [USB\_LOCK.stl](./stl_files/other/USB_LOCK.stl) | [USB\_LOCK.obj](./obj_files/other/USB_LOCK.obj) |
| P34 | Vaccum funnel | 1 | vaccum_funnel | [VACUUM\_FUNNEL.stl](./stl_files/router/VACUUM_FUNNEL.stl) | [VACUUM\_FUNNEL.obj](./obj_files/router/VACUUM_FUNNEL.obj) |
| P35 | Vaccum hose ring | 1 | vaccum_hose_ring | [VACUUM\_HOSE\_RING.stl](./stl_files/router/VACUUM_HOSE_RING.stl) | [VACUUM\_HOSE\_RING.obj](./obj_files/router/VACUUM_HOSE_RING.obj) |
| P36 | Vertical carriage slider | 1 | vertical_carriage_slider | [VERTICAL\_SLIDER.stl](./stl_files/router/VERTICAL_SLIDER.stl) | [VERTICAL\_SLIDER.obj](./obj_files/router/VERTICAL_SLIDER.obj) |
| P37 | Wasteboard bracket | 7 |  | [BRACKET.stl](./stl_files/other/BRACKET.stl) | [BRACKET.obj](./obj_files/other/BRACKET.obj) |
| P38 | X-axis cable chain mount | 1 | x_axis_cable_chain_mount | [CABLE\_CHAIN\_MOUNT.stl](./stl_files/router/CABLE_CHAIN_MOUNT.stl) | [CABLE\_CHAIN\_MOUNT.obj](./obj_files/router/CABLE_CHAIN_MOUNT.obj) |
| P39 | Z-axis end-stop trigger | 1 | z_limit_trigger | [Z\_END\_STOP\_TRIGGER.stl](./stl_files/other/Z_END_STOP_TRIGGER.stl) | [Z\_END\_STOP\_TRIGGER.obj](./obj_files/other/Z_END_STOP_TRIGGER.obj) |
| P40 | Z-axis stepper motor mount | 1 | z_motor_mount | [Z\_MOTOR\_MOUNT.stl](./stl_files/router/Z_MOTOR_MOUNT.stl) | [Z\_MOTOR\_MOUNT.obj](./obj_files/router/Z_MOTOR_MOUNT.obj) |

## Screws

| Item No. | Size  | Length | Amount | Image |
|---|---|---|---|---|
| S01 | 3.5mm | 20mm | 14 | 3-5mm_20mm |
| S02 | M3 | 12mm | 20 | M3_12mm |
| S03 | M3 | 16mm | 96 | M3_16mm |
| S04 | M3 | 20mm | 32 | M3_20mm |
| S05 | M3 | 25mm | 36 | M3_25mm |
| S06 | M3 | 40mm | 12 | M3_40mm |
| S07 | M3 | 5mm | 8 | M3_5mm |
| S08 | M3 | 8mm | 4 | M3_8mm |
| S09 | M4 | 18mm | 2 | M4_18mm |
| S10 | M4 | 25mm | 19 | M4_25mm |
| S11 | M4 | 40mm | 8 | M4_40mm |
| S12 | M5 | 20mm | 26 | M5_20mm |
| S13 | M5 | 40mm | 6 | M5_40mm |
| S14 | M5 | 60mm | 2 | M5_60mm |
| S17 | M5 | 80mm | 1 | M5_80mm |
| S15 | M8 | 60mm | 9 | M8_60mm |
| S16 | M8 | 80mm | 2 | M8_80mm |

## Nuts

| Item No. | Size | Amount | Image |
|---|---|---|---|
| N01 | M4 | 11 | M4 |
| N02 | M5 | 15 | M5 |
| N03 | M8 | 35 | M8 |

## Washers

| Item No. | Outer diameter | Inner diameter | Thickness | Amount | Image |
|---|---|---|---|---|---|
| W01 | 10mm | 5mm | 1mm | 13 | 10mm_5mm_1mm |
| W02 | 15mm | 5mm | 1mm | 14 | 15mm_5mm_1mm |
| W03 | 15mm | 8.5mm | 1.5mm | 24 | 15mm_8-5mm_1-5mm |
| W04 | 20mm | 10mm | 2mm | 27 | 20mm_10mm_2mm |
| W05 | 8mm | 4mm | 0.5mm | 12 | 8mm_4mm_0-5mm |
| W06 | 8mm | 4mm | 1mm | 4 | 8mm_4mm_1mm |
| W07 | 9mm | 4.5mm | 1mm | 2 | 9_4-5_1mm |

## Electronics

| Item No. | Type | Amount | Image |
|---|---|---|---|
| E01 | 12V Fan | 2 | fan |
| E02 | 12V power supply (UHP-200-12) | 1 | power_supply |
| E03 | 12V wires (black and red) | ~10m | 12V_cable |
| E04 | 220V power plug | 1 | power_plug |
| E05 | 220V power socket | 1 | power_socket |
| E06 | 220V/10A cable (red, blue and green/yellow) | ~2m | 220V_cable |
| E07 | 3-way Wago splicing connector (221-413) | 3 | 3-way_wago_splicing_connector |
| E08 | AWG22 wire (red, blue, green and black) | ~10m per color | awg22_wire |
| E09 | Arduino Uno | 1 | Arduino_Uno |
| E10 | Arduino Uno CNC Shield | 1 | CNC_shield |
| E11 | Bipolar stepper motor (Nema 17, no gear, 5mm shaft diameter) | 1 | NEMA17_no_gears |
| E12 | C-GRID III contact housing, 2.54mm (1X2) | 5 | Missing |
| E13 | C-GRID III contact housing, 2.54mm (1X4) | 4 | contact_housing |
| E14 | C14 terminal | 1 | c14_terminal |
| E15 | Crimp sleeve C-GRID III AWG 22/24 | 26 | crimp_sleeve |
| E16 | DRV8825 stepper drivers | 4 | stepper_drivers |
| E17 | Emergency stop switch (KJD17B) | 1 | emergency_stop_switch |
| E18 | Geared (19:1) bipolar stepper motor (Nema 17, 8mm shaft diameter) | 3 | NEMA17_geared |
| E19 | Jumpers | 6 | jumpers |
| E20 | Makita RT0700C (milling router) | 1 | milling_router |
| E21 | Microswitch | 5 | microswitch |
| E22 | Red LED | 1 | red_led |
| E23 | Ring terminal (M3) | 4 | ring_terminal_M3 |
| E24 | Ring terminal (M4) | 3 | ring_terminal_M4 |
| E25 | Spade connector (2.8mm) | 10 | spade_connector_2-8mm |
| E26 | Spade connector (4.8mm) | 6 | spade_connector_4-8mm |
| E27 | Spade connector (6.3mm) | 4 | spade_connector_6-3mm |
| E28 | USB A (male) to USB B (male) | 1 | USB_A_to_USB_B |
| E29 | USB A PCB (female) | 1 | usb_a_female |
| E30 | C13 cable | 1 | c13_cable |

## Threaded rods

| Item No. | Size | Length | Amount | Image |
|---|---|---|---|---|
| T01 | M5 | 140mm  | 2 | threaded_rod_M5_140_mm |
| T02 | M8 | 120mm  | 8 | threaded_rod_M8_120_mm |
| T03 | M8 | 717mm  | 4 | threaded_rod_M8_717_mm |

## Other

| | Type | Amount | Image |
|-----|---|---|---|
| O01 | 698zz bearing | 18 | 698zz_bearing |
| O02 | Acme threaded rod (300 mm long, 8x8mm) | 1 | acme_threaded_rod |
| O03 | Acme threaded rod nut (8x8mm) | 1 | acme_nut |
| O04 | Aluminium profiles (677x30x30 mm) | 4 | aluminium_profiles_677mm_30mm_30mm |
| O05 | Aluminium profiles (803x30x30 mm) | 3 | aluminium_profiles_803mm_30mm_30mm |
| O06 | Aluminium profiles (80x30x30 mm) | 8 | aluminium_profiles_80mm_30mm_30mm |
| O07 | Aluminium profiles (900x30x30 mm) | 4 | aluminium_profiles_900mm_30mm_30mm |
| O08 | Braided cable sleeve (20mm) | 5m | cable_sleeve |
| O09 | Cable chain (1m long, 30x15mm inner dimensions) | 2 | cable_chain |
| O10 | Cable clip | 1 | cable_clip |
| O11 | Cable ties | ~30 | cable_ties |
| O12 | Flat end mill | NA | flat_end_mills |
| O13 | Flexible conduit | 2m | cable_conduit |
| O14 | GT2 belt (6mm belt width, 300mm long) | 1 | 2GT_belt_300_mm |
| O15 | GT2 pulley (16 teeth, 5mm bore, 6mm belt width) | 1 | 2GT_pulley_16_teeth |
| O16 | GT2 pulley (60 teeth, 8mm bore, 6mm belt width) | 1 | 2GT_pulley_60_teeth |
| O17 | HTD5M belt (15mm width) | 4m | HTD5M_belt |
| O18 | HTD5M pulley (12 teeth, 8mm bore, 15mm belt width) | 3 | HTD5M_pulley |
| O19 | KFL08 rod bearing (8mm) | 2 | KFL08_rod_bearing |
| O20 | MGN12H linear rail (200mm) | 2 | MGN12H_rail_200_mm |
| O21 | MGN12H linear rail (600mm) | 4 | MGN12H_rail_600_mm |
| O22 | MGN12H linear rail block | 12 | MGN12H_rail_block |
| O23 | Masking tape | 1 | masking_tape |
| O24 | Shrinking tubes | NA | shrinking_tubes |
| O25 | Cable grommet | 1 | cable_grommet |
| O26 | Plywood (approx. 12x1500x1500mm) | 1 | plywood |
| O27 | Brush | 0.5m | dust_shoe |

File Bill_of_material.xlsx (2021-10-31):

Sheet: Aggregated - Bill of material
Screws
Item No. | Size | Length | Amount
S01 | 3.5mm | 20mm | 14
S02 | M3 | 12mm | 20
S03 | M3 | 16mm | 96
S04 | M3 | 20mm | 32
S05 | M3 | 25mm | 36
S06 | M3 | 40mm | 12
S07 | M3 | 5mm | 8
S08 | M3 | 8mm | 4
S09 | M4 | 18mm | 2
S10 | M4 | 25mm | 19
S11 | M4 | 40mm | 8
S12 | M5 | 20mm | 26
S13 | M5 | 40mm | 6
S14 | M5 | 60mm | 2
S15 | M8 | 60mm | 9
S16 | M8 | 80mm | 2
Nuts
Item No. | Size | Amount
N01 | M4 | 11
N02 | M5 | 14
N03 | M8 | 35
Washers
Item No. | Outer diameter | Inner diameter | Thickness | Amount
W01 | 10mm | 5mm | 1mm | 13
W02 | 15mm | 5mm | 1mm | 14
W03 | 15mm | 8.5mm | 1.5mm | 24
W04 | 20mm | 10mm | 2mm | 27
W05 | 8mm | 4mm | 0.5mm | 12
W06 | 8mm | 4mm | 1mm | 4
W07 | 9mm | 4.5mm | 1mm | 2
Electronics
Item No. | Type | Amount
E01 | 12V Fan | 2
E02 | 12V power supply (UHP-200-12) | 1
E03 | 12V wires (black and red)
E04 | 220V power plug | 1
E05 | 220V power socket | 1
E06 | 220V/10A cable (red, blue and green/yellow)
E07 | 3-way Wago splicing connector (221-413) | 3
E08 | AWG22 wire (red, blue, green and black)
E09 | Arduino Uno | 1
E10 | Arduino Uno CNC Shield | 1
E11 | Bipolar stepper motor (Nema 17, no gear, 5mm shaft diameter) | 1
E12 | C-GRID III contact housing, 2.54mm (1X2) | 5
E13 | C-GRID III contact housing, 2.54mm (1X4) | 4
E14 | C14 terminal | 1
E15 | Crimp sleeve C-GRID III AWG 22/24 | 26
E16 | DRB8825 stepper drivers | 4
E17 | Emergency stop switch (KJD17B) | 1
E18 | Geared (19:1) bipolar stepper motor (Nema 17, 8mm shaft diameter) | 3
E19 | Jumpers | 6
E20 | Makita RT0700C (milling router) | 1
E21 | Microswitch | 5
E22 | Red LED | 1
E23 | Ring terminal (M3) | 4
E24 | Ring terminal (M4) | 3
E25 | Spade connector (2.8mm) | 10
E26 | Spade connector (4.8mm) | 6
E27 | Spade connector (6.3mm) | 4
E28 | USB A (male) to USB B (male) | 1
E29 | USB A PCB (female) | 1
E30 | C13 cable | 1
3d-printed parts
Item No. | Type | Amount
P01 | Back middle panel (large electronic box) | 1
P02 | Back middle panel (small electronic box) | 1
P03 | Back panel (large electronic box) | 1
P04 | Back panel (small electronic box) | 1
P05 | Cable chain mount | 1
P06 | Cable chain support | 1
P07 | Carriage | 1
P08 | End-stop mount (ordinary) | 3
P09 | End-stop mount (tall) | 1
P10 | End-stop mount (thick) | 1
P11 | Flexible conduit strain relief (halves) | 8
P12 | Front middle panel (large electronic box) | 1
P13 | Front middle panel (small electronic box) | 1
P14 | Front panel (large electronic box) | 1
P15 | Front panel (small electronic box) | 1
P16 | Idler block | 3
P17 | Left belt tension slider | 1
P18 | Left belt tensioner | 1
P19 | Left fixed belt tensioner | 1
P20 | Left side plate | 1
P21 | Left side plate lower back clip | 1
P22 | Left side plate lower front clip | 1
P23 | Left side plate upper front clip | 1
P24 | Milling router bracket | 1
P25 | Rail support | 3
P26 | Right belt tension slider | 1
P27 | Right belt tensioner | 2
P28 | Right fixed belt tensioner | 2
P29 | Right side plate | 1
P30 | Right side plate lower back clip | 1
P31 | Right side plate lower front clip | 1
P32 | Right side plate upper front clip | 1
P33 | USB lock | 1
P34 | Vaccum funnel | 1
P35 | Vaccum hose ring | 1
P36 | Vertical carriage slider | 1
P37 | Wasteboard bracket | 7
P38 | X-axis cable chain mount | 1
P39 | Z-axis end-stop trigger | 1
P40 | Z-axis stepper motor mount | 1
Other
Item No. | Type | Amount
O01 | 698zz bearing | 18
O02 | Acme threaded rod (300 mm long, 8x8mm) | 1
O03 | Acme threaded rod nut (8x8mm) | 1
O04 | Aluminium profiles (677x30x30 mm) | 4
O05 | Aluminium profiles (803x30x30 mm) | 3
O06 | Aluminium profiles (80x30x30 mm) | 8
O07 | Aluminium profiles (900x30x30 mm) | 4
O08 | Braided cable sleeve (20mm)
O09 | Cable chain (1m long, 30x15mm inner dimensions) | 2
O10 | Cable clip | 1
O11 | Cable ties
O12 | Flat end mill
O13 | Flexible conduit
O14 | GT2 belt (6mm belt width, 300mm long) | 1
O15 | GT2 pulley (16 teeth, 5mm bore, 6mm belt width) | 1
O16 | GT2 pulley (60 teeth, 8mm bore, 6mm belt width) | 1
O17 | HTD5M belt (15mm width)
O18 | HTD5M pulley (12 teeth, 8mm bore, 15mm belt width) | 3
O19 | KFL08 rod bearing (8mm) | 2
O20 | MGN12H linear rail (200mm) | 2
O21 | MGN12H linear rail (600mm) | 4
O22 | MGN12H linear rail block | 12
O23 | Masking tape | 1
O24 | Shrinking tubes
O25 | Cable grommet | 1
O26 | Plywood (approx. 12x1500x1500mm) | 1
Threaded rods
Item No. | Size | Length | Amount
T01 | M5 | 140mm | 2
T02 | M8 | 120mm | 8
T03 | M8 | 717mm | 4

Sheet: Raw - Bill of material
Raw item list
Screws
Item No. | Category | Used in | Type | Size | Length | Amount | Used for | Comment | Image?
S11 | Consumables | Large electronic box | Screws | M4 | 40mm | 4 | Used in the front of the large electronic box |  | X
S09 | Consumables | Large electronic box | Screws | M4 | 18mm | 2 | Used to lock the emergency stop switch to the large electronic box |  | X
S07 | Consumables | Large electronic box | Screws | M3 | 5mm | 4 | Used to lock power supply to back panel of the large electronic box | The spare 4x 5mm M3 screws locking the gear box to the stepper motors was used. | X
S10 | Consumables | Large electronic box | Screws | M4 | 25mm | 4 | Used in the back of the large electronic box |  | X
S02 | Consumables | Large electronic box | Screws | M3 | 12mm | 4 | Used to lock fan to front plate of large electronic box |  | X
S11 | Consumables | Small electronic box | Screws | M4 | 40mm | 4 | Used in the front of the small electronic box |  | X
S10 | Consumables | Small electronic box | Screws | M4 | 25mm | 4 | Used in the back of the small electronic box |  | X
S02 | Consumables | Small electronic box | Screws | M3 | 12mm | 4 | Used to lock fan to front plate of small electronic box |  | X
S07 | Consumables | Small electronic box | Screws | M3 | 5mm | 4 | Used to lock Arduino to back panel of the small electronic box |  | X
S01 | Consumables | Frame | Screws | 3.5mm | 20mm | 14 | Used to interlock wasteboard and frame, using the wasteboard brackets |  | X
S10 | Consumables | Frame | Screws | M4 | 25mm | 2 | Used to interlock the cable chain mount with the cable chain |  | X
S12 | Consumables | Frame | Screws | M5 | 20mm | 2 | Used to lock cable chain mount with frame |  | X
S12 | Consumables | Frame | Screws | M5 | 20mm | 2 | Used to lock left Y-axis belt tension slider to frame |  | X
S15 | Consumables | Frame | Screws | M8 | 60mm | 1 | Used to tension the left Y-axis belt | Buy a fully threaded screw | X
S12 | Consumables | Frame | Screws | M5 | 20mm | 2 | Used to lock Y-axis end-stop (-) mount to frame |  | X
S02 | Consumables | Frame | Screws | M3 | 12mm | 2 | Used to lock Y-axis end-stop (-) microswitch to end-stop mount |  | X
S03 | Consumables | Frame | Screws | M3 | 16mm | 24 | Used to lock left Y-axis MGN12H linear rail to frame |  | X
S04 | Consumables | Frame | Screws | M3 | 20mm | 8 | Used to lock left side plate to left Y-axis MGN12H linear rail blocks |  | X
S12 | Consumables | Frame | Screws | M5 | 20mm | 2 | Used to lock cable chain support to frame |  | X
S12 | Consumables | Frame | Screws | M5 | 20mm | 2 | Used to lock left Y-axis fixed belt tensioner to frame |  | X
S12 | Consumables | Frame | Screws | M5 | 20mm | 2 | Used to lock left Y-axis end-stop (+) mount to frame |  | X
S02 | Consumables | Frame | Screws | M3 | 12mm | 2 | Used to lock Y-axis end-stop (+) microswitch to end-stop mount |  | X
S12 | Consumables | Frame | Screws | M5 | 20mm | 2 | Used to tension the right Y-axis belt |  | X
S15 | Consumables | Frame | Screws | M8 | 60mm | 1 | Used to tension the right Y-axis belt | Buy a fully threaded screw | X
S12 | Consumables | Frame | Screws | M5 | 20mm | 2 | Used to tension the right Y-axis belt |  | X
S12 | Consumables | Frame | Screws | M5 | 20mm | 2 | Used to lock right Y-axis end-stop mount to frame (only used to block linear rail) |  | X
S03 | Consumables | Frame | Screws | M3 | 16mm | 24 | Used to lock right Y-axis MGN12H linear rail to frame |  | X
S04 | Consumables | Frame | Screws | M3 | 20mm | 8 | Used to lock right side plate to right Y-axis MGN12H linear rail blocks |  | X
S06 | Consumables | Bridge | Screws | M3 | 40mm | 4 | Used to lock right geared stepper motor to right side plate |  | X
S15 | Consumables | Bridge | Screws | M8 | 60mm | 2 | Used in right Y-axis belt idler | Buy fully threaded screws | X
S15 | Consumables | Bridge | Screws | M8 | 60mm | 2 | Used in left Y-axis belt idler | Buy fully threaded screws | X
S06 | Consumables | Bridge | Screws | M3 | 40mm | 4 | Used to lock left geared stepper motor to left side plate |  | X
S10 | Consumables | Bridge | Screws | M4 | 25mm | 2 | Used to interlock the left side plate with the cable chain |  | X
S14 | Consumables | Bridge | Screws | M5 | 60mm | 1 | Used to lock left side plate, left side plate upper front clip and upper front bridge aluminium profile. | It doesn't hurt to buy a longer screw, e.g. 65 or 70mm | X
S14 | Consumables | Bridge | Screws | M5 | 60mm | 1 | Used to lock right side plate, right side plate upper front clip and upper front bridge aluminium profile. | It doesn't hurt to buy a longer screw, e.g. 65 or 70mm | X
S15 | Consumables | Bridge | Screws | M8 | 60mm | 1 | Used to tension the X-axis belt | Buy fully threaded screws | X
S12 | Consumables | Bridge | Screws | M5 | 20mm | 2 | Used to tension the X-axis belt |  | X
S12 | Consumables | Bridge | Screws | M5 | 20mm | 2 | Used to lock X-axis end-stop (-) mount to lower front aluminium bridge profile |  | X
S02 | Consumables | Bridge | Screws | M3 | 12mm | 2 | Used to lock X-axis end-stop (-) microswitch to end-stop mount |  | X
S03 | Consumables | Bridge | Screws | M3 | 16mm | 24 | Used to lock lower X-axis MGN12H linear rail to lower bridge bream aluminium profile |  | X
S03 | Consumables | Bridge | Screws | M3 | 16mm | 24 | Used to lock upper X-axis MGN12H linear rail to upper bridge bream aluminium profile |  | X
S13 | Consumables | Bridge | Screws | M5 | 40mm | 2 | Used to lock X-axis end-stop (+) mount to upper front aluminium bridge profile |  | X
S02 | Consumables | Bridge | Screws | M3 | 12mm | 2 | Used to lock X-axis end-stop (+) microswitch to end-stop mount |  | X
S10 | Consumables | Bridge | Screws | M4 | 25mm | 2 | Used to interlock the X-axis cable chain with the lower back bridge beam aluminium profile |  | X
S10 | Consumables | Bridge | Screws | M4 | 25mm | 2 | Used to interlock the X-axis cable chain with the cable chain mount on carriage |  | X
S10 | Consumables | Bridge | Screws | M4 | 25mm | 3 | Used to lock X-axis cable chain mount to Z-axis stepper motor mount |  | X
S08 | Consumables | Bridge | Screws | M3 | 8mm | 4 | Used to lock Z-axis stepper motor to Z-axis stepper motor mount |  | X
S16 | Consumables | Bridge | Screws | M8 | 80mm | 2 | Used to lock Z-axis stepper motor mount to carriage |  | X
S12 | Consumables | Bridge | Screws | M5 | 20mm | 2 | Used to lock KFL08 rod bearing to top of carriage |  | X
S12 | Consumables | Bridge | Screws | M5 | 20mm | 2 | Used to lock KFL08 rod bearing to bottom of carriage |  | X
S05 | Consumables | Bridge | Screws | M3 | 25mm | 8 | Used to lock carriage to lower X-axis MGN12H linear rail blocks |  | X
S05 | Consumables | Bridge | Screws | M3 | 25mm | 8 | Used to lock carriage to upper X-axis MGN12H linear rail blocks |  | X
S06 | Consumables | Bridge | Screws | M3 | 40mm | 4 | Used to lock X-axis geared stepper motor to carriage |  | X
S15 | Consumables | Bridge | Screws | M8 | 60mm | 2 | Used in X-axis belt idler | Buy fully threaded screws | X
S02 | Consumables | Bridge | Screws | M3 | 12mm | 2 | Used to lock Z-axis end-stop (+) microswitch to carriage |  | X
S05 | Consumables | Bridge | Screws | M3 | 25mm | 4 | Lock acme nut to vertical carriage slider |  | X
S02 | Consumables | Bridge | Screws | M3 | 12mm | 2 | Used to lock Z-axis end-stop (+) trigger to vertical carriage slider |  | X
S05 | Consumables | Bridge | Screws | M3 | 25mm | 8 | Used to lock MGN12H linear rail blocks to right side of carriage (Z-axis) |  | X
S05 | Consumables | Bridge | Screws | M3 | 25mm | 8 | Used to lock MGN12H linear rail blocks to left side of carriage (Z-axis) |  | X
S04 | Consumables | Bridge | Screws | M3 | 20mm | 8 | Used to lock left 200mm MGN12H linear rail to vertical carriage slider (Z-axis) |  | X
S04 | Consumables | Bridge | Screws | M3 | 20mm | 8 | Used to lock right 200mm MGN12H linear rail to vertical carriage slider (Z-axis) |  | X
S13 | Consumables | Bridge | Screws | M5 | 40mm | 4 | Used to lock router bracket to vertical carriage slider |  | X
Nuts
Item No. | Category | Used in | Type | Size | Amount | Used for | Comment | Image?
N01 | Consumables | Large electronic box | Nuts | M4 | 2 | Used to lock the emergency stop switch to the large electronic box |  | X
N03 | Consumables | Frame | Nuts | M8 | 8 | Used to interlock aluminium profiles (upper and lower frame) | Buy lock nut if available | X
N03 | Consumables | Frame | Nuts | M8 | 16 | Used to interlock lower and upper frame | Buy lock nut if available | X
N01 | Consumables | Frame | Nuts | M4 | 2 | Used to interlock the cable chain mount with the cable chain |  | X
N03 | Consumables | Frame | Nuts | M8 | 1 | Used to tension the left Y-axis belt | Buy lock nut if available | X
N03 | Consumables | Frame | Nuts | M8 | 1 | Used to tension the right Y-axis belt | Buy lock nut if available | X
N03 | Consumables | Bridge | Nuts | M8 | 2 | Used in right Y-axis belt idler | Buy ordinary nuts, as lock nuts won't fit in the holes in the side plate | X
N03 | Consumables | Bridge | Nuts | M8 | 2 | Used in left Y-axis belt idler | Buy ordinary nuts, as lock nuts won't fit in the holes in the side plate | X
N01 | Consumables | Bridge | Nuts | M4 | 2 | Used to interlock the left side plate with the cable chain |  | X
N02 | Consumables | Bridge | Nuts | M5 | 1 | Used to lock left side plate, left side plate upper front clip and upper front bridge aluminium profile. |  | X
N02 | Consumables | Bridge | Nuts | M5 | 2 | Used to lock left side plate, left side plate lower front/back clip and lower front/back bridge aluminium profile. |  | X
N02 | Consumables | Bridge | Nuts | M5 | 1 | Used to lock right side plate, right side plate upper front clip and upper front bridge aluminium profile. |  | X
N02 | Consumables | Bridge | Nuts | M5 | 2 | Used to lock right side plate, right side plate lower front/back clip and lower front/back bridge aluminium profile. |  | X
N03 | Consumables | Bridge | Nuts | M8 | 1 | Used to tension X-axis belt | Buy lock nut if available | X
N01 | Consumables | Bridge | Nuts | M4 | 2 | Used to interlock the X-axis cable chain with the cable chain mount on carriage |  | X
N01 | Consumables | Bridge | Nuts | M4 | 3 | Used to lock X-axis cable chain mount to Z-axis stepper motor mount |  | X
N03 | Consumables | Bridge | Nuts | M8 | 2 | Used to lock Z-axis stepper motor mount to carriage |  | X
N02 | Consumables | Bridge | Nuts | M5 | 2 | Used to lock KFL08 rod bearing to top of carriage |  | X
N02 | Consumables | Bridge | Nuts | M5 | 2 | Used to lock KFL08 rod bearing to bottom of carriage |  | X
N03 | Consumables | Bridge | Nuts | M8 | 2 | Used in X-axis belt idler | Buy ordinary nuts, as lock nuts won't fit in the holes in the side plate | X
N02 | Consumables | Bridge | Nuts | M5 | 4 | Used to lock router bracket to vertical carriage slider |  | X
Washers
Item No. | Category | Used in | Type | Outer diameter | Inner diameter | Thickness | Amount | Comment | Comment/adjustment if you can't find exact piece | Image?
W07 | Consumables | Large electronic box | Washers | 9mm | 4.5mm | 1mm | 2 | Used to lock the emergency stop switch to the large electronic box |  | X
W02 | Consumables | Frame | Washers | 15mm | 5mm | 1mm | 14 | Used to interlock wasteboard and frame, using the wasteboard brackets |  | X
W04 | Consumables | Frame | Washers | 20mm | 10mm | 2mm | 8 | Used to interlock aluminium profiles (upper and lower frame) |  | X
W04 | Consumables | Frame | Washers | 20mm | 10mm | 2mm | 16 | Used to interlock upper and lower frame |  | X
W01 | Consumables | Frame | Washers | 10mm | 5mm | 1mm | 2 | Used to interlock the cable chain mount with the Y-axis cable chain |  | X
W04 | Consumables | Frame | Washers | 20mm | 10mm | 2mm | 1 | Used to tension the left Y-axis belt |  | X
W04 | Consumables | Frame | Washers | 20mm | 10mm | 2mm | 1 | Used to tension the right Y-axis belt |  | X
W05 | Consumables | Bridge | Washers | 8mm | 4mm | 0.5mm | 4 | Used to lock right geared stepper motor to right side plate |  | X
W03 | Consumables | Bridge | Washers | 15mm | 8.5mm | 1.5mm | 8 | Used in right Y-axis belt idler | Don't buy a too big outer diameter, as it might limit the movement of the bearings. | X
W03 | Consumables | Bridge | Washers | 15mm | 8.5mm | 1.5mm | 8 | Used in left Y-axis belt idler | Don't buy a too big outer diameter, as it might limit the movement of the bearings. | X
W05 | Consumables | Bridge | Washers | 8mm | 4mm | 0.5mm | 4 | Used to lock left geared stepper motor to left side plate |  | X
W01 | Consumables | Bridge | Washers | 10mm | 5mm | 1mm | 2 | Used to interlock the left side plate with the Y-axis cable chain |  | X
W01 | Consumables | Bridge | Washers | 10mm | 5mm | 1mm | 2 | Used to interlock the X-axis cable chain with the cable chain mount on carriage |  | X
W01 | Consumables | Bridge | Washers | 10mm | 5mm | 1mm | 3 | Used to lock X-axis cable chain mount to Z-axis stepper motor mount |  | X
W06 | Consumables | Bridge | Washers | 8mm | 4mm | 1mm | 4 | Used to lock Z-axis stepper motor to Z-axis stepper motor mount |  | X
W04 | Consumables | Bridge | Washers | 20mm | 10mm | 2mm | 1 | Used to lock Z-axis stepper motor mount to carriage |  | X
W05 | Consumables | Bridge | Washers | 8mm | 4mm | 0.5mm | 4 | Used to lock X-axis geared stepper motor to carriage |  | X
W03 | Consumables | Bridge | Washers | 15mm | 8.5mm | 1.5mm | 8 | Used in X-axis belt idler | Don't buy a too big outer diameter, as it might limit the movement of the bearings. | X
W01 | Consumables | Bridge | Washers | 10mm | 5mm | 1mm | 4 | Used to lock router bracket to vertical carriage slider |  | X
Electronics
Item No. | Category | Used in | Type | Amount | Used for | Comment | Comment/adjustment if you can't find exact piece | Image?
E17 | Electronics | Large electronic box | Emergency stop switch (KJD17B) | 1 | Used to switch of all power in emergencies |  | • Left hole in large electronic box's front plate • 6.3mm splicing connector to whatever fits your emergency stop switch | X
E01 | Electronics | Large electronic box | 12V Fan | 1 | Used to blow air out of the large electronic box | 12V DC, 100mA, 40x40x10 mm | Screw hole profile and fan grid on the back side of the large electronic box's front plate | X
E22 | Electronics | Large electronic box | Red LED | 1 | Used to indicate that the power is on | 12V DC. 8mm diameter | LED hole in large electronic box's front plate | X
E14 | Electronics | Large electronic box | C14 terminal | 1 | Used to connect C13 power cable to power the CNC | Recommend to buy one with a built in fuse (e.g. glass fuse) | • Right hole in large electronic box's front plate • 4.8mm splicing connector to whatever fits your C14 terminal | X
E27 | Electronics | Large electronic box | Spade connector (6.3mm) | 4 | Used to connect power to and from emergency stop switch | Recommended to buy 2 blue and 2 red to follow electrical color code | Dependent on emergency stop switch | X
E26 | Electronics | Large electronic box | Spade connector (4.8mm) | 6 | Used to connect power wires from C14 terminal | Recommended to buy 3 red, 2 blue and 1 green/yellow to follow electrical color code | Dependent on C14 terminal | X
E06 | Electronics | Large electronic box | 220V/10A cable (red, blue and green/yellow) | ~2m | Used to wire 220V between C14 terminal, emergency stop switch and power supply | Make sure that you buy cable that can handle 220V. Also, I recommend to buy stranded cable as a solid cable might be more difficult to use. |  | X
E07 | Electronics | Large electronic box | 3-way Wago splicing connector (221-413) | 3 | Used to split 220V inside large electronic box |  | Any 3-way splicing connector works, as long as it's graded for the 220V wires | X
E02 | Electronics | Large electronic box | 12V power supply (UHP-200-12) | 1 | Converts 220V to 12V (200.4W, 16.7A) |  | • Hole profile on the large electronic box's back plate • Make sure that it outputs 12 V and has enought amps for your steppers etc. | X
E24 | Electronics | Large electronic box | Ring terminal (M4) | 3 | Used to connect 220V to power supply | Recommended to buy 1 red, 1 blue and one green/yellow to follow electrical color code | Dependent on power supply | X
E23 | Electronics | Large electronic box | Ring terminal (M3) | 4 | Used to output 12V from power supply | Recommended to buy 2 red and 2 blue to follow electrical color code | Dependent on power supply | X
E01 | Electronics | Small electronic box | 12V Fan | 1 | Used to blow air out of the small electronic box | 12V DC, 100mA, 40x40x10 mm | Screw hole profile and fan grid on the back side of the small electronic box's front plate | X
E29 | Electronics | Small electronic box | USB A PCB (female) | 1 | Used to connect USB cable to Arduino |  | USB hole in small electronic box's front plate | X
E28 | Electronics | Small electronic box | USB A (male) to USB B (male) | 1 | Connects USB A PCB (female) to Arduino | 30 cm should be more than enough |  | X
E03 | Electronics | Other | 12V wires (black and red) | ~10m | Used for all end-stops and for power between power supply and CNC shield | Make sure that the cable is graded for the voltage and amps required |  | X
E16 | Electronics | Small electronic box | DRB8825 stepper drivers | 4 | Used by all 4 stepper motors (X, Y1, Y2 and Z) |  | Make sure that the stepper drivers fits the Arduino CNC shield | X
E10 | Electronics | Small electronic box | Arduino Uno CNC Shield | 1 | Chip that is used between the Arduino and the stepper motors |  | Make sure that the CNC shield fits the Arduino Uno | X
E09 | Electronics | Small electronic box | Arduino Uno | 1 | Runs GRBL and executes all the G-Code sent by the computer |  | There are clones of the Arduino Uno as well | X
E19 | Electronics | Small electronic box | Jumpers | 6 | Used to set microstepping on CNC shield and to mirror Y-axis | Buy more than 6 if you want to have the option to set other microstepping | As long as you can short the pins, it doesn't matter | X
E13 | Electronics | Small electronic box | C-GRID III contact housing, 2.54mm (1X4) | 4 | Housing used when connecting stepper motors to CNC shield |  | Make sure that they fit the crimp sleeve | X
E12 | Electronics | Small electronic box | C-GRID III contact housing, 2.54mm (1X2) | 5 | Housing used when connecting end-stops to CNC shield |  | Make sure that they fit the crimp sleeve
E15 | Electronics | Small electronic box | Crimp sleeve C-GRID III AWG 22/24 | 26 | Crimped on top of each stepper motor and end-stop wire | Recommended to buy more than 26, as you will probably waste a couple of them in the process | Make sure that they fit the contact housing | X
E08 | Electronics | Other | AWG22 wire (red, blue, green and black) | ~10m per color | Used to extend the stepper motor wires |  | Make sure that the cable fit the voltage/amps you're planning to use | X
E25 | Electronics | Frame | Spade connector (2.8mm) | 2 | Used to connect Y-axis end-stop (-) wires to microswitch (end-stop) | Recommended to buy 1 red and 1 black to follow electrical color code |  | X
E21 | Electronics | Frame | Microswitch | 1 | Used as Y-axis end-stop (-) | Search word: V4 Miniature Microswitch (roller lever) | Adjust holes in end-stop mount | X
E25 | Electronics | Frame | Spade connector (2.8mm) | 2 | Used to connect Y-axis end-stop (+) wires to microswitch (end-stop) | Recommended to buy 1 red and 1 black to follow electrical color code |  | X
E21 | Electronics | Frame | Microswitch | 1 | Used as Y-axis end-stop (+) | Search word: V4 Miniature Microswitch (roller lever) | Adjust holes in end-stop mount | X
E18 | Electronics | Bridge | Geared (19:1) bipolar stepper motor (Nema 17, 8mm shaft diameter) | 1 | Used as rigth Y-axis stepper motor | Search words: Nema 17 Stepper Motor Bipolar L=48mm w/ Gear Ratio 19:1 Planetary Gearbox | Adjust right side plate and pulley inner diameter | X
E18 | Electronics | Bridge | Geared (19:1) bipolar stepper motor (Nema 17, 8mm shaft diameter) | 1 | Used as left Y-axis stepper motor | Search words: Nema 17 Stepper Motor Bipolar L=48mm w/ Gear Ratio 19:1 Planetary Gearbox | Adjust right side plate and pulley inner diameter | X
E25 | Electronics | Bridge | Spade connector (2.8mm) | 2 | Used to connect X-axis end-stop (-) wires to microswitch (end-stop) | Recommended to buy 1 red and 1 black to follow electrical color code |  | X
E21 | Electronics | Bridge | Microswitch | 1 | Used as X-axis end-stop (-) | Search word: V4 Miniature Microswitch (roller lever) | Adjust holes in end-stop mount | X
E25 | Electronics | Bridge | Spade connector (2.8mm) | 2 | Used to connect X-axis end-stop (+) wires to microswitch (end-stop) | Recommended to buy 1 red and 1 black to follow electrical color code |  | X
E21 | Electronics | Bridge | Microswitch | 1 | Used as X-axis end-stop (+) | Search word: V4 Miniature Microswitch (roller lever) | Adjust holes in end-stop mount | X
E04 | Electronics | Bridge | 220V power plug | 1 | Used for cable management of milling router | Either buy a normal power plug, or if you can find a Neutrik powercon plug (and socket) that can handle 220V |  | X
E05 | Electronics | Bridge | 220V power socket | 1 | Used for cable management of milling router | Either buy a normal power socket, or if you can find a Neutrik powercon socket (and plug) that can handle 220V |  | X
E11 | Electronics | Bridge | Bipolar stepper motor (Nema 17, no gear, 5mm shaft diameter) | 1 | Used as Z-axis stepper motor | Search words: Nema 17 Bipolar 1.8deg 45Ncm (64oz.in) 1.68A 2.8V 42x42x48mm 4 Wires |  | X
E18 | Electronics | Bridge | Geared (19:1) bipolar stepper motor (Nema 17, 8mm shaft diameter) | 1 | Used as X-axis stepper motor | Search words: Nema 17 Stepper Motor Bipolar L=48mm w/ Gear Ratio 19:1 Planetary Gearbox |  | X
E25 | Electronics | Bridge | Spade connector (2.8mm) | 2 | Used to connect Z-axis end-stop (+) wires to microswitch (end-stop) | Recommended to buy 1 red and 1 black to follow electrical color code |  | X
E21 | Electronics | Bridge | Microswitch | 1 | Used as Z-axis end-stop (+) | Search word: V4 Miniature Microswitch (roller lever) |  | X
E20 | Electronics | Bridge | Makita RT0700C (milling router) | 1 | Used as the milling router |  | There's an alternative named Makita RT0700CJ that also works | X
E30 | Electronics | Bridge | C13 cable | 1 | Used to power the CNC machine |  |  | X
3d-printed
Item No. | Category | Used in | Type | Amount | Used for | Comment | Comment/adjustment if you can't find exact piece | Image? | STL | OBJ
P14 | 3d-printed | Large electronic box | Front panel (large electronic box) | 1 | Front panel of large electronic box |  |  | X
P12 | 3d-printed | Large electronic box | Front middle panel (large electronic box) | 1 | Front middle panel of large electronic box |  |  | X
P01 | 3d-printed | Large electronic box | Back middle panel (large electronic box) | 1 | Back middle panel of large electronic box
P03 | 3d-printed | Large electronic box | Back panel (large electronic box) | 1 | Back panel of large electronic box |  |  | X
P11 | 3d-printed | Other | Flexible conduit strain relief (halves) | 8 | Used to strain relief flexible conduits (large and small electronic boxes) |  | Adjust inner diameter if you can't find a 13mm cable conduit | X
P15 | 3d-printed | Small electronic box | Front panel (small electronic box) | 1 | Front panel of small electronic box |  |  | X
P13 | 3d-printed | Small electronic box | Front middle panel (small electronic box) | 1 | Front middle panel of small electronic box |  |  | X
P02 | 3d-printed | Small electronic box | Back middle panel (small electronic box) | 1 | Back middle panel of small electronic box |  |  | X
P04 | 3d-printed | Small electronic box | Back panel (small electronic box) | 1 | Back panel of small electronic box |  |  | X
P33 | 3d-printed | Small electronic box | USB lock | 1 | Used to lock the USB A female to the small electronic box's front panel |  | Adjust inner measurements depending on the USB A female | X
P25 | 3d-printed | Other | Rail support | 3 | Used to lock the rails into place on the Aluminium profiles | Designed for 30x30mm aluminium profiles |  | X
P37 | 3d-printed | Frame | Wasteboard bracket | 7 | Used to interlock wasteboard and frame | Designed for 30x30mm aluminium profiles |  | X
P05 | 3d-printed | Frame | Cable chain mount | 1 | Used to interlock frame and Y-axis cable chain |  | Adjust holes based on cable chain holes | X
P06 | 3d-printed | Frame | Cable chain support | 1 | Used to support Y-axis cable chain |  |  | X
P17 | 3d-printed | Frame | Left belt tension slider | 1 | Used to tension the left Y-axis belt |  |  | X
P18 | 3d-printed | Frame | Left belt tensioner | 1 | Used to tension the left Y-axis belt |  |  | X
P08 | 3d-printed | Frame | End-stop mount (ordinary) | 1 | Used for Y-axis end-stop (-) and block left Y-axis linear rail |  | Adjust holes if other microswitch hole profiles | X
P19 | 3d-printed | Frame | Left fixed belt tensioner | 1 | Used to tension the left Y-axis belt |  |  | X
P09 | 3d-printed | Frame | End-stop mount (tall) | 1 | Used for Y-axis end-stop (+) |  |  | X
P26 | 3d-printed | Frame | Right belt tension slider | 1 | Used to tension the right Y-axis belt |  |  | X
P27 | 3d-printed | Frame | Right belt tensioner | 1 | Used to tension the right Y-axis belt |  |  | X
P28 | 3d-printed | Frame | Right fixed belt tensioner | 1 | Used to tension the right Y-axis belt |  |  | X
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

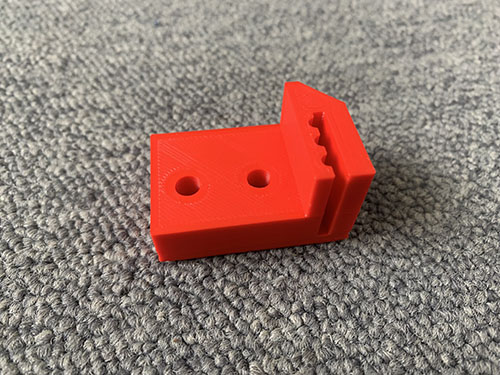
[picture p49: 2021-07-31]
images/3dprinted_parts/belt_tensioner/x_axis/x_axis_back_clip.jpg

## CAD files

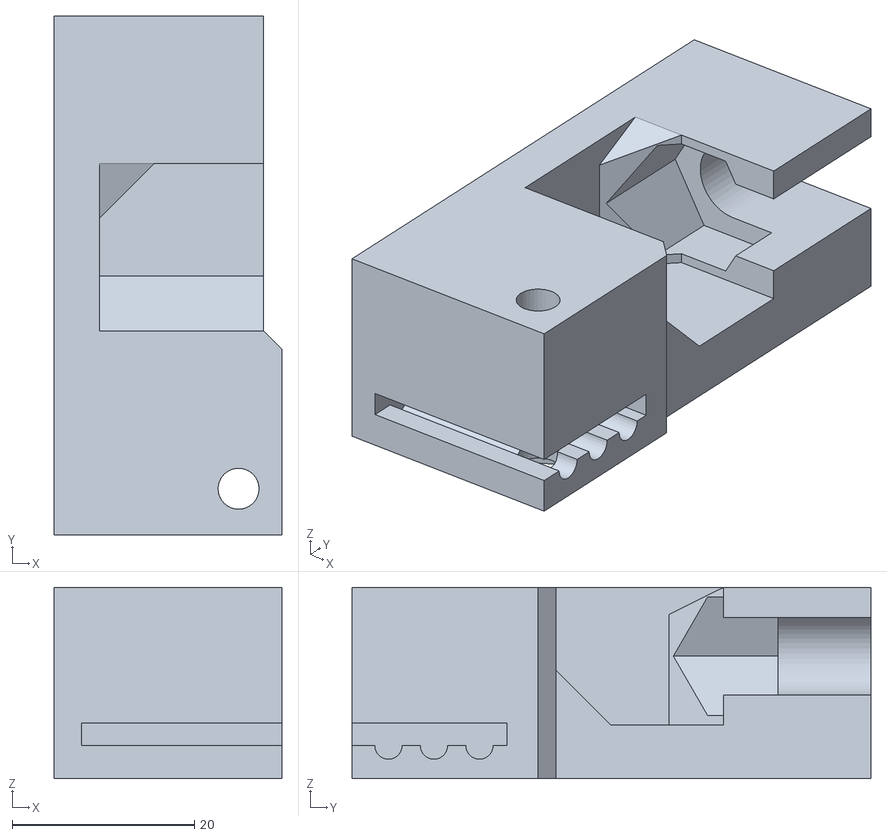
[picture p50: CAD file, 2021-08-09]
stl_files/belt_tensioner/x_axis/X_AXIS_FRONT_CLIP.stl
25.0 x 57.0 x 21.0

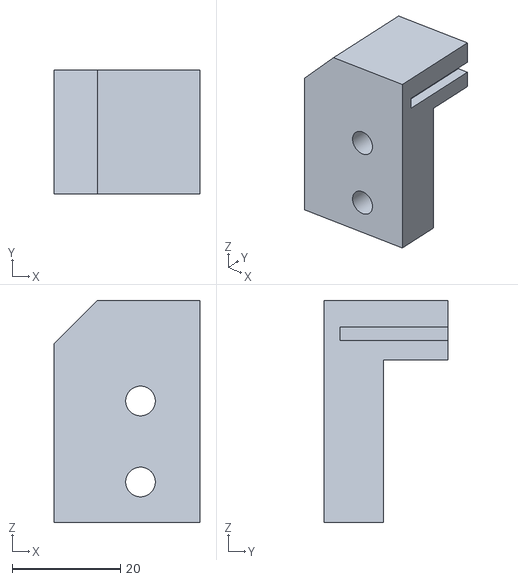
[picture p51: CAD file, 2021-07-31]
stl_files/belt_tensioner/y_axis_left/Y_AXIS_LEFT_BACK_CLIP.stl
27.0 x 23.0 x 41.1

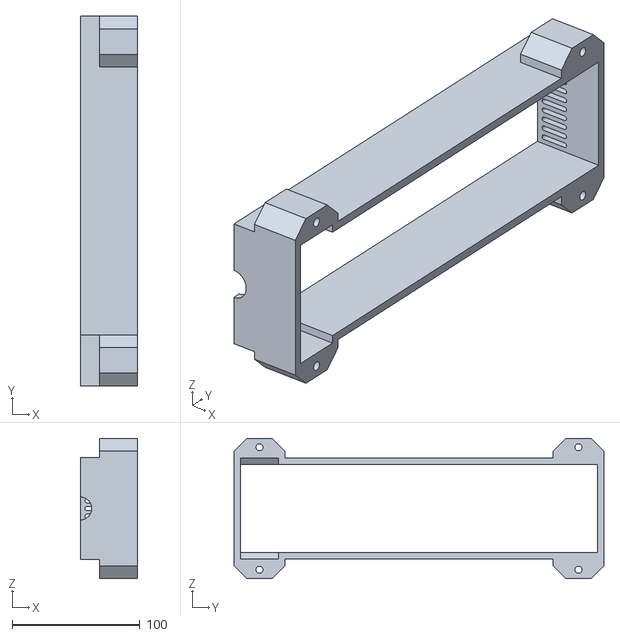
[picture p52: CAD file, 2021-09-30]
stl_files/electronic_box_large/middle_front_panel_electronic_box_large.stl
45.0 x 290.0 x 110.0

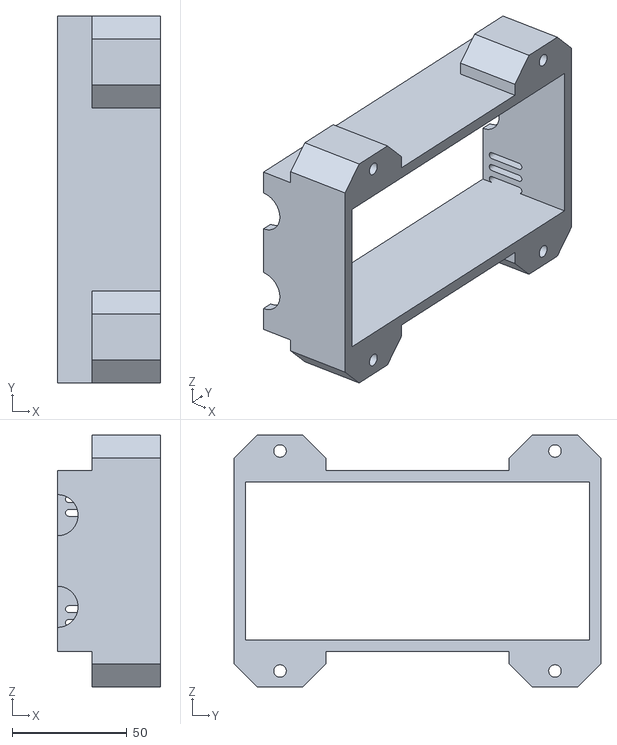
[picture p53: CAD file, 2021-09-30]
stl_files/electronic_box_small/middle_front_panel_electronic_box_small.stl
45.0 x 160.0 x 110.0

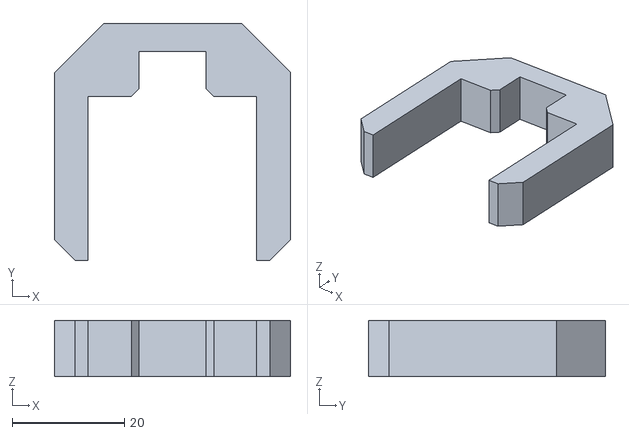
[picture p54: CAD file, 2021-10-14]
stl_files/other/RAILS_SUPPORT.stl
42.0 x 42.1 x 10.0

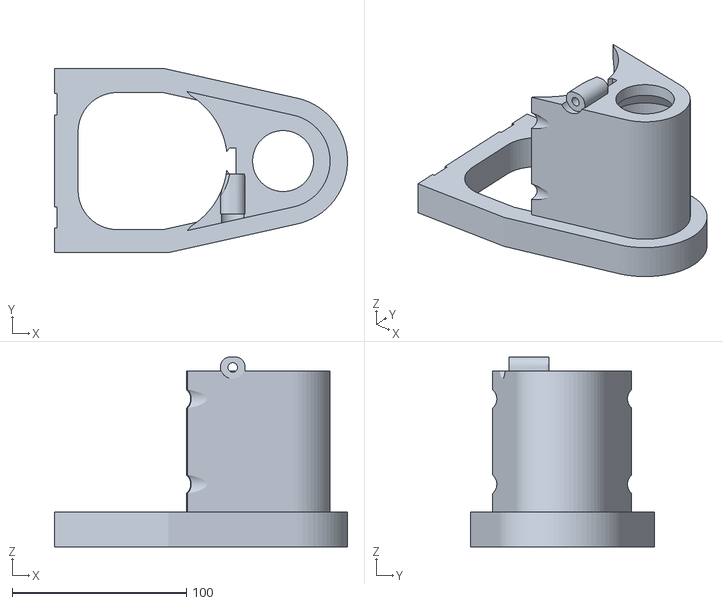
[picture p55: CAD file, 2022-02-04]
stl_files/router/VACUUM_FUNNEL.stl
168.1 x 105.8 x 109.0

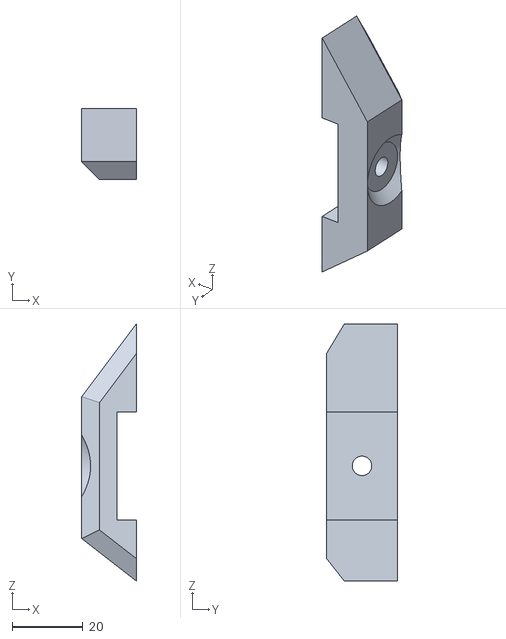
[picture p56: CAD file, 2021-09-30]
stl_files/side_plates/left/LEFT_PLATE_BACK_CLIP.stl
15.4 x 20.0 x 72.5

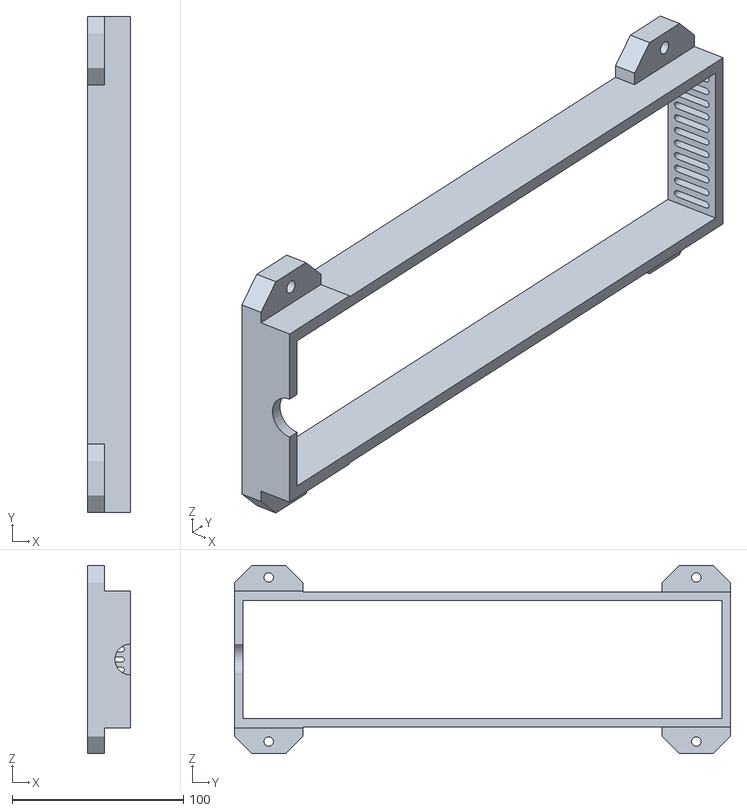
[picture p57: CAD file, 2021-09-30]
stl_files/electronic_box_large/middle_back_panel_electronic_box_large.stl
25.0 x 290.0 x 110.0

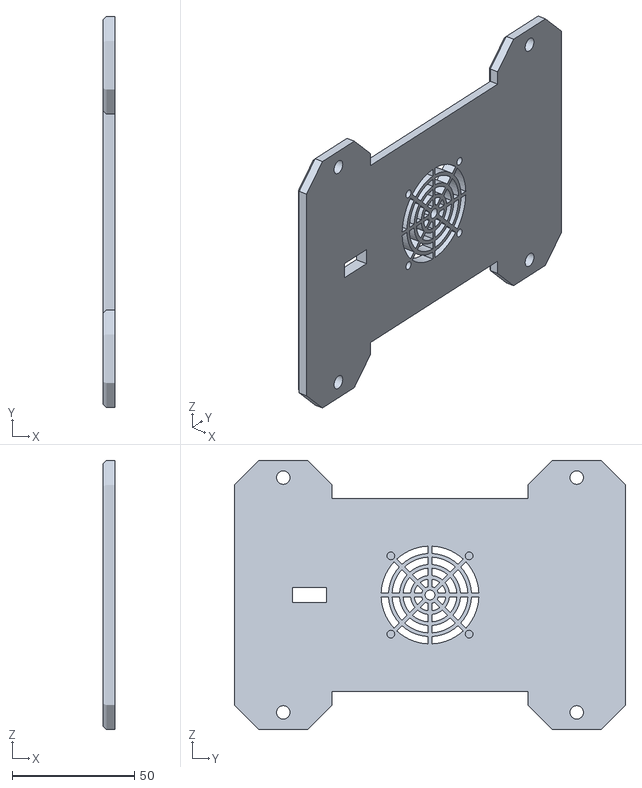
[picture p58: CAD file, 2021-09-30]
stl_files/electronic_box_small/front_panel_electronic_box_small.stl
5.00 x 160.0 x 110.0

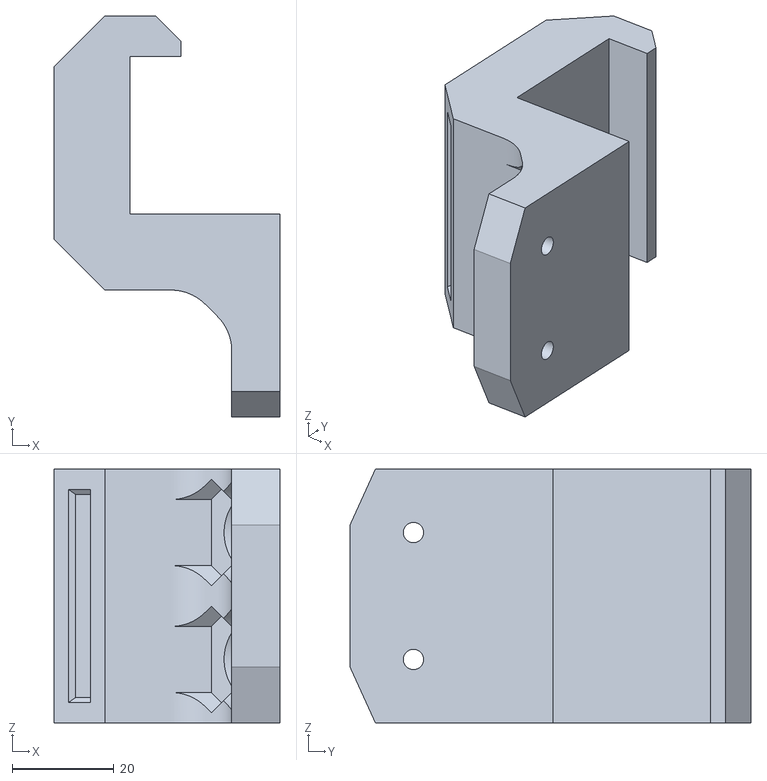
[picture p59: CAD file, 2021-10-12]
stl_files/other/BRACKET.stl
44.5 x 79.0 x 50.0

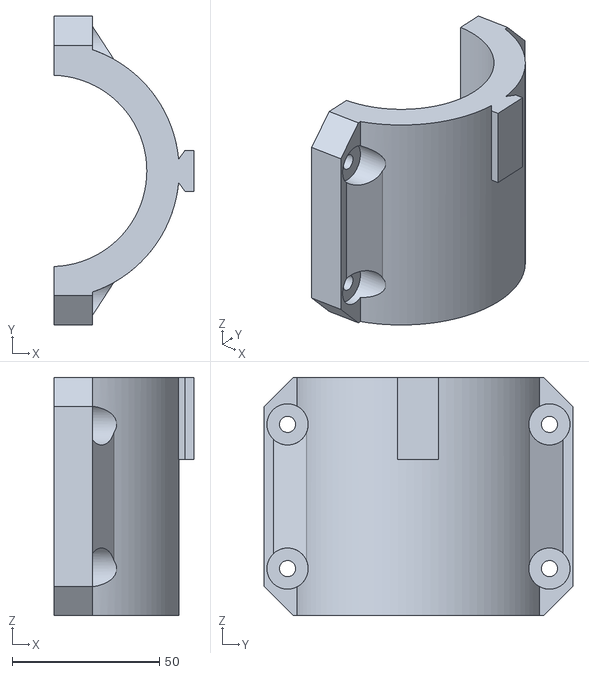
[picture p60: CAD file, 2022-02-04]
stl_files/router/ROUTER_BRACKET.stl
47.5 x 105.0 x 81.0

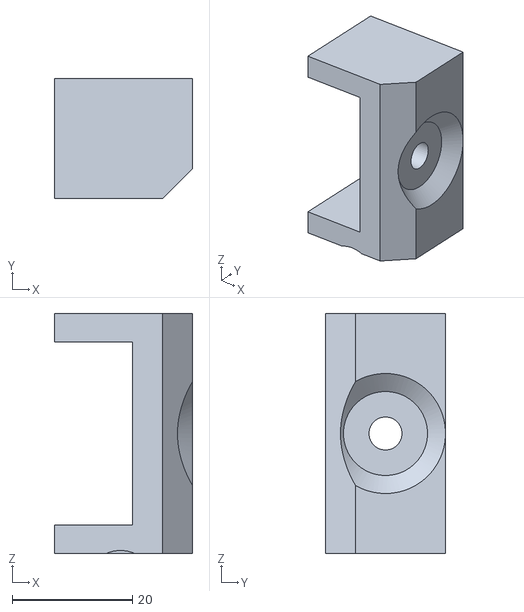
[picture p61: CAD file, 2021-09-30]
stl_files/side_plates/left/LEFT_PLATE_LOWER_FRONT_CLIP.stl
23.0 x 20.0 x 40.0

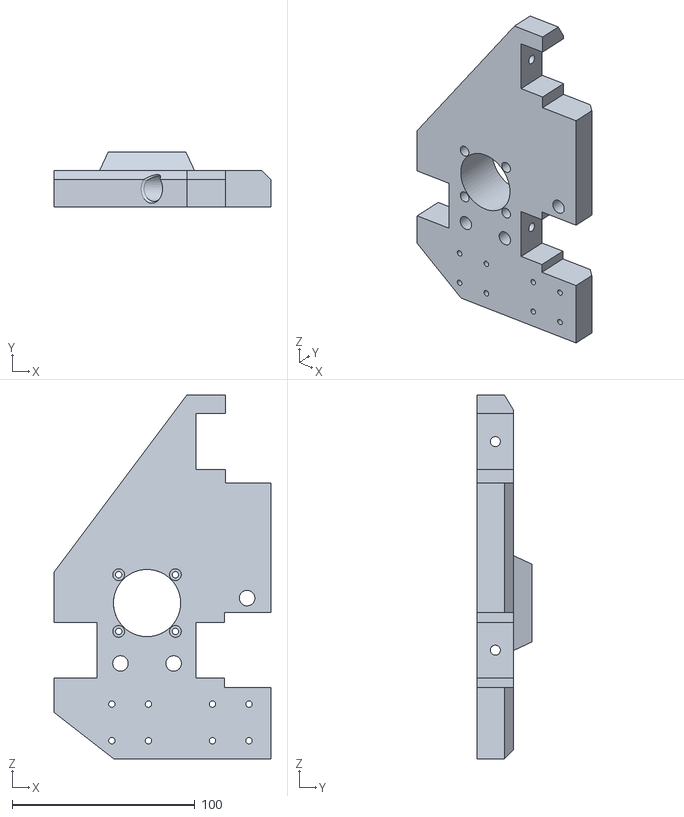
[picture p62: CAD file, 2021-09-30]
stl_files/side_plates/right/RIGHT PLATE.stl
118.6 x 30.0 x 199.0

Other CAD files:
stl_files/belt_tensioner/y_axis_right/Y_AXIS_RIGHT_FRONT_CLIP.stl
stl_files/side_plates/right/RIGHT_PLATE_BACK_CLIP.stl
stl_files/belt_tensioner/x_axis/X_AXIS_BACK_CLIP.stl
stl_files/belt_tensioner/y_axis_left/Y_AXIS_LEFT_FRONT_CLIP.stl
stl_files/belt_tensioner/y_axis_right/Y_AXIS_RIGHT_BACK_CLIP.stl
obj_files/belt_tensioner/x_axis/X_AXIS_BACK_CLIP.obj
obj_files/belt_tensioner/x_axis/X_AXIS_FRONT_CLIP.obj
obj_files/belt_tensioner/y_axis_left/Y_AXIS_LEFT_BACK_CLIP.obj
obj_files/belt_tensioner/y_axis_left/Y_AXIS_LEFT_BELT_TENSIONER.obj
obj_files/belt_tensioner/y_axis_left/Y_AXIS_LEFT_FRONT_CLIP.obj
obj_files/belt_tensioner/y_axis_right/Y_AXIS_RIGHT_BACK_CLIP.obj
obj_files/belt_tensioner/y_axis_right/Y_AXIS_RIGHT_BELT_TENSIONER.obj
obj_files/belt_tensioner/y_axis_right/Y_AXIS_RIGHT_FRONT_CLIP.obj
obj_files/electronic_box_large/back_panel_electronic_box_large.obj
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

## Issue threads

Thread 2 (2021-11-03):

Approximate cost?

cweagans, 2021-11-03:
If I was going to build this, what would the approximate materials cost be?

maxvfischer, 2021-11-03:
I ended up paying around $1100 in total, but then I paid for the fastest shipping, ordered some parts that I ended up not using and spent 3d-printing filament on parts I had to redesign and reprint. So I would say between $600-$1500 depending on where your source the parts from (Aliexpress or high-end website), how fast you want it delivered, where you live etc.

Closed 2023-10-28.

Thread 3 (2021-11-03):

[enhancement] Laser engraving

damajor, 2021-11-03:
Add some support for laser engraving head :)

maxvfischer, 2021-11-04:
There are actually a guy in the Discord-channel that I wrote about in the readme that has done that exact adjustment. Might look into it myself when I got time. Can ask him if I can upload his design and .STL-files.

Closed 2023-10-28.

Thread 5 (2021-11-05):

Expansion

KingWeasel76, 2021-11-05:
Is it possible to increase the x & y axis for this build? I'm thinking to utilise it for a full sheet size.

maxvfischer, 2021-11-07:
To extend the X-axis and Y-axis, you need to increase the length of the aluminium profiles and buy longer MGN12H rails. I'm not sure if it's possible to build a machine that is able to cut full sheets with the current design, as you probably won't find MGN12H rails that large, and I'm not sure that it's a good idea to link them up.

But Ivan Miranda has designed a CNC machine able to cut full sheets, maybe you can get some inspiration from that: https://www.youtube.com/watch?v=d6Sx95dOuvI

maxvfischer, 2023-10-28:
I'm closing this issue due to inactivity.

Closed 2023-10-28.

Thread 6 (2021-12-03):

Print parameters

pgrudzien1987, 2021-12-03:
Is somewhere information about print parameters for 3d elements? I mean infill percentage for instance.
Also what kind of material do you recommended? PLA/PETG?

maxvfischer, 2021-12-04:
I just pushed my PrusaSlicer config to the repo and added information about infill etc to the BOM.

I printed everything in PLA, using the folloing settings:

- 30% infill
- 4 top solid horizontal layers
- 4 bottom solid horizontal layers
- 4 perimeters

Closed 2021-12-05.

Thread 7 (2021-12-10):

Request step CAD format

jack9603301, 2021-12-10:
I use freecad. Because you don't provide a step file format in line with industry specifications, I don't have software to open it. Can you request the body

maxvfischer, 2021-12-10:
Hey!

Do I understand you correctly that you want all the 3d-printable parts in ".step" format?

jack9603301, 2021-12-11:
Yes, including the overall assembly drawing, just like the f3z file you provided, I cannot open it, so I need a step format file.

maxvfischer, 2021-12-11:
**Regarding the assembly drawings**
Sorry to say, but there are no overall assembly drawings. This is a DIY hobby project that I've done on my spare time. As I'm new to mechanical engineer, I didn't even know that assembly drawings were a standard thing. But you're more than welcome to create them and create a pull request :)

**Regarding the step format files**
Alright! I'm currenly busy with a lot of other things, but I'll try to do it when I got some more time :) In the mean time, you can always download Fusion360 (it's free) and open the f3z file.

jack9603301, 2021-12-11:
Can Fusion360 be used under Linux? I can't even download it. . Weird network.

maxvfischer, 2021-12-13:
I'm not sure, think you have to resort to Google for that one :)

maxvfischer, 2023-10-28:
I'm closing this issue due to inactivity.

Closed 2023-10-28.

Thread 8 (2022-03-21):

How to make US version?

tenumars, 2022-03-21:
The title is pretty self-explanatory, is there a way to get the drill and other parts in USA format? And if so, do any of the parts need to be changed for the different voltage? Thanks

tenumars, 2022-03-21:
In just looking for the router, in case anyone is having the same issue, I found a US version on amazon
[https://us.amazon.com/gp/product/B00E7D3V4S/ref=ox_sc_act_title_1?smid=ATVPDKIKX0DER&th=1](url)
Not an affiliate link

maxvfischer, 2022-03-22:
Hey! When buying Ivan's blueprints, he includes .STL-files adjusted for inches and common american parts (square tubes etc). Also, you'll get access to a Discord channel with people who have built the machine, and I would guess that some of them have used the american .STL-files and measurements.

So I would recommend you to buy the blueprints for $25 and then ask all the questions in the Discord channel. People are really helpful there :)

Link to blueprints: https://ivanmiranda.com/products/3d-printed-cnc

tenumars, 2022-10-11:
<!--
/* Font Definitions */
@font-face
	{font-family:"Cambria Math";
	panose-1:2 4 5 3 5 4 6 3 2 4;}
@font-face
	{font-family:Calibri;
	panose-1:2 15 5 2 2 2 4 3 2 4;}
/* Style Definitions */
p.MsoNormal, li.MsoNormal, div.MsoNormal
	{margin:0in;
	font-size:11.0pt;
	font-family:"Calibri",sans-serif;}
a:link, span.MsoHyperlink
	{mso-style-priority:99;
	color:blue;
	text-decoration:underline;}
.MsoChpDefault
	{mso-style-type:export-only;}
@page WordSection1
	{size:8.5in 11.0in;
	margin:1.0in 1.0in 1.0in 1.0in;}
div.WordSection1
	{page:WordSection1;}
-->Ok, thanks, will do! From: Max FischerSent: Tuesday, March 22, 2022 5:49 AMTo: maxvfischer/DIY-CNC-machineCc: tenumars; AuthorSubject: Re: [maxvfischer/DIY-CNC-machine] How to make US version? (Issue #8) Hey! When buying Ivan's blueprints, he includes .STL-files adjusted for inches and common american parts (square tubes etc). Also, you'll get access to a Discord channel with people who have built the machine, and I would guess that some of them have used the american .STL-files and measurements.So I would recommend you to buy the blueprints for $25 and then ask all the questions in the Discord channel. People are really helpful there :)Link to blueprints: https://ivanmiranda.com/products/3d-printed-cnc—Reply to this email directly, view it on GitHub, or unsubscribe.You are receiving this because you authored the thread.Message ID: ***@***.***>

Closed 2023-10-28.

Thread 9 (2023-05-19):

wrong direction

hahsjs, 2023-05-19:
hi. im realy new to this project. im using a stepper motor nema 17 bipolar, and it's running on a wrong direction. if i clicked the right button on universal gcode sender, the machine is running to up-left direction. if i clicked the up-left, it's running to right. hope someone can help me with this

maxvfischer, 2023-05-22:
It's difficult to assess what the exact problem is without knowing more. This could happen if you accidentally swap the cables to the stepper motor. Have you double-checked that they are attached correctly to the shield?

maxvfischer, 2023-10-28:
Closing this issue due to inactivity.

Closed 2023-10-28.

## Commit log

2021-07-31 Add stl-files
    [CARRIAGE.stl, HTD5M LEFT BACK CLIP.stl, HTD5M LEFT FRONT CLIP WITH M4 BOLT INSERT.stl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]
2021-07-31 Update file names
    [LEFT_PLATE_BACK_CLIP.stl, LEFT_PLATE_LOWER_FRONT_CLIP.stl, LEFT_PLATE_UPPER_FRONT_CLIP.stl]
2021-07-31 Remove old files
    [LEFT PLATE BACK CLIP.stl, LEFT PLATE LOWER FRONT CLIP.stl, LEFT PLATE UPPER FRONT CLIP.stl]
2021-07-31 Add left side plate table
2021-07-31 Update image path left plate
2021-07-31 Update left side plate table
2021-07-31 Add right plate table
2021-07-31 Update stl links right plate table
2021-07-31 Rename stl-files
    [RIGHT_PLATE.stl, RIGHT_PLATE_BACK_CLIP.stl, RIGHT_PLATE_LOWER_FRONT_CLIP.stl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]
2021-07-31 Update names router images
    [ROUTER_BRACKET.stl, VACUUM_FUNNEL.stl, VERTICAL_SLIDER.stl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]
2021-07-31 Add row to router table
    [VACUUM_HOSE_RING.stl]
2021-07-31 Update belt tensioner stl file names
    [X_AXIS_BACK_CLIP.stl, X_AXIS_FRONT_CLIP.stl, Y_AXIS_LEFT_BACK_CLIP.stl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]
2021-07-31 Add belt tensioner images
2021-07-31 Add belt tensioner table
2021-07-31 Add images of building main frame
2021-07-31 Add text about building the main frame
2021-09-06 Add arrows to frame image
2021-09-30 Update stl right plate
    [RIGHT_PLATE.stl]
2021-09-30 Add stl small electronics box
    [back_middle_panel.stl, back_plate.stl, front_middle_panel.stl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]
2021-09-30 Add stl large electronic mox
    [back_middle_panel.stl, back_plate.stl, front_middle_panel.stl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]
2021-09-30 Add other stl files
    [CABLE_LOCK.stl, ENDSTOP_LIMIT_SWITCH.stl, ENDSTOP_LIMIT_SWITCH_LONG.stl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]
2021-09-30 Add y-axis cable chain mount stl
    [CABLE_CHAIN_MOUNT.stl]
2021-09-30 Update left plate image
2021-09-30 Update left plate STLs
    [LEFT_PLATE.stl, LEFT_PLATE_BACK_CLIP.stl, LEFT_PLATE_LOWER_FRONT_CLIP.stl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]
2021-09-30 Update right side plate stls
    [RIGHT PLATE.stl, RIGHT_PLATE.stl, RIGHT_PLATE_BACK_CLIP.stl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]
2021-09-30 Update name of right side plate stl
    [RIGHT_PLATE.stl]
2021-09-30 Update right side plate README
2021-10-11 Update names of electronic boxes stl files
    [back_panel.stl, front_panel.stl, middle_back_panel.stl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]
2021-10-12 Add and update names of stl-files
    [BRACKET.stl, CABLE_STRAIN_RELIEF.stl, IDLER_BLOCK.stl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]
2021-10-12 Add other 3d-printed parts to README
2021-10-12 Update name of z limit trigger
    [Z_END_STOP_TRIGGER.stl]
2021-10-14 Add Rail support image
2021-10-14 Add Rails support stl
    [RAILS_SUPPORT.stl]
2021-10-26 Add bill of material markdown
2021-10-26 Update BOM
2021-10-27 Add .stl files as .obj (the ones that are available)
    [CABLE_CHAIN_MOUNT.obj, CABLE_STRAIN_RELIEF.obj, CARRIAGE.obj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]
2021-10-27 Update name of electronic boxes' names
    [back_panel_electronic_box_large.stl, back_panel_electronic_box_small.stl, front_panel_electronic_box_large.stl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]
2021-10-27 Add obj to BOM
2021-10-27 Update names of electronic box obj files
    [back_panel_electronic_box_large.obj, back_panel_electronic_box_small.obj, front_panel_electronic_box_large.obj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]
2021-10-27 Add BOM spreadsheet
    [Bill_of_material.xlsx]
2021-10-27 Add Fusion360 raw cad-files
2021-10-31 Add image of C13 cable
2021-10-31 Add c13 cable to BOM
2021-10-31 Add cable grommet image
2021-10-31 Add cable grommet to BOM
2021-10-31 Add pywood to BOM
2021-10-31 Update excel-version of BOM
    [Bill_of_material.xlsx]
2021-12-04 Add PrusaSlicer config file and text to BOM
2021-12-04 Add filament used to BOM
2022-02-04 Add image of 80mm M5 screw
2022-02-04 Update STL and OBJ of router bracket
    [ROUTER_BRACKET.obj, ROUTER_BRACKET.stl]
2022-02-04 Update STL and OBJ of vaccum funnel
    [VACUUM_FUNNEL.obj, VACUUM_FUNNEL.stl]
2022-02-04 Add dust shoe parts to Bill of material
